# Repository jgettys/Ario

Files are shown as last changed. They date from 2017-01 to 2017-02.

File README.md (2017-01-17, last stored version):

# Ario

This is the mechanical design for ATMoB's ARIO 10' diameter telescope
dome.  It was designed by Charlie Gettys in the spring of 2016, and
fabricated by Charlie & Jim Gettys and Bruce Berger.  Note that we are
currently designing a radio controlled motor controller as a companion
to this mechanical design.

The design opens or closes the dome slit in approximately 30 seconds in
ideal circumstances.

Note: the specified threaded rod was ordered by mistake: it is gross
overkill for the application; something much cheaper can/should be
bought rather than the precision rod currently specified in the as
built BOM. And the corresponding nut used should also be much cheaper.

It may take 50-100lbs force to start the slit of 10' dome ATMoB
has; we may decide to improve the cable path on our dome using pully
sheaves (as many of the later versions of that dome already have
improved designs) to reduce the required force.

The clutch in the design should prevent over stressing of the cable.
The cable has an operating strength of about 90lbs, with a breaking
strength about five times higher.  The motor was sized to provide enough
torque to produce about 100lbs of force given the diameter of the
threaded rod.

The design could be adapted/scaled up for much larger dome slits or
roll off roofs, by choosing other motors or changing the gear ratio in
the drive.  The gearing used with the motor was deliberately chosen to
have that flexibility, and the motor itself is available in different
sizes.  The components are easily available and "standard" among the
FIRST robotics community.

There is a included spreadsheet for making the torque
computations. Note that the motor, gear box, cable and threaded rod
all interact to produce the desired speed and force to move the dome
slit.

This design could be scaled up by using larger threaded rods and cables.
The force and closing speed can also be changed over a significant range
by changing the gearing in the gear box.  The ARIO gear design order
is documented in the file "motorspec.txt".

At maximum torque, you should not choose a motor that will generate
more force than the operating strength of the chosen cable. The clutch
is intended to provide a "fail safe" such that the breaking strength
of the cable will never be reached.

At maximum torque of one of these motors, you may need to provide
significant current; 55 amps@12V for the chosen motor in the ARIO design.

We are currently designing a radio controlled remote dome motor
controller to go with this mechanical design to replace our existing
current limited power supply (which cannot provide enough current),
which will be driven by a deep cycle marine battery charged by a solar
panel on the dome, to avoid needing power transfer to the dome, which
may not be designed into most smaller domes. A battery can easily
provide the needed current for the limited time to open or close the
dome more easily than a power supply.

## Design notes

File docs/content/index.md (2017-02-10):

---
date: 2017-02-08T21:07:13+01:00
title: ATMoB Domus Dome Controller
type: index
weight: 0
---

## Modern, Open Source Design

Domus is a modern dome control system, intended to enable fully
automatic operation of a modern telescope, based on an elaboration of
the excellent work of Gerry Rozema's [NexDome system](https://github.com/grozzie2/NexDome).

Domus is very inexpensive and adaptable and is built from widely available components and all software and firmware is open source.

## Features

* "Fail Safe" operation: Domus is designed to enable safe unattended operation of a telescope. As such, the observatory must "fail safe" in case of:
    * Rain or mist conditions
    * Excessive Wind
    * Dewing conditions
* Adaptability to local telescope system
    * Wireless slit controller, enabling battery powered operation of the slit closing mechanism; no power and the dome will still be safed
    * Dome control via [ASCOM](http://ascom-standards.org), for Windows users
    * Dome control via [Indi](http://indilib.org/), for Linux and MacIntosh users
    * Dome control and customization via Web application
* Adaptability to a large variety of weather equipment, by using the [WeeWX](http://www.weewx.com/) software package
    * These include a large variety of USB weather stations, as well as some Ethernet based weather stations.
    * Custom rain/mist sensor, for "fail safe" operation of the dome

See the [getting started guide]({{< relref "getting-started/index.md" >}}) for instructions how to get
Domus up and running.

## Components

* Dome Slit Opening/Closing Mechanism
* Dome Rotation Mechanism
* Dome control electronics
* WeeWX weather software
* Weather station (select appropriate station from those supported by WeeWX)
* Raspberry Pi controller
    * To enable integration of the WeeWX weather system,
    * remote dome control,
    * interior and exterior cameras,
    * "fail safe" operation, so that malfunction of the telescope computer will not inhibit safing of the telescope.
    * (optional) local GPS stratum zero NTP server, to provide good time to the local observing environment
* Raspbian OS, configured for "headless" remote use via ssh or web operation
  
## Acknowledgements

Gerry Rozema designed the excellent [NexDome controller](https://github.com/grozzie2/NexDome)

Charlie Gettys designed the dome slit mechanism, with kibitzing from Jim Gettys, Alan Sliski, and [Bruce Berger](http://www.medomakretreatcenter.com/bruceberger.php).

[Alan Sliski](http://www.theskyscrapers.org/alan-sliski) designed the dome rotation mechanism and encoder, and the electronics for controlling the slit and dome, and integrated the weather sensor.

[Jim Gettys](https://en.wikipedia.org/wiki/Jim_Gettys) put together the control server, based on a Raspberry Pi, the WeeWX software, and glue.

The Web site design is due to the Hugo site generator, using the Material docs theme.

Furthermore, thanks to [Steve Francia](https://gihub.com/spf13) for creating Hugo and the [awesome community](https://github.com/spf13/hugo/graphs/contributors) around the project.

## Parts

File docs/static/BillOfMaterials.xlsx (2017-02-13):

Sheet: Dome Slit Mechanism
Name | Link | Unit Cost | Quantity | Total Cost | Notes
Mechanical:
100:1 Versa Planetary Gearbox with BAG Motor | http://www.vexrobotics.com/vexpro/motion/gearboxes/versaplanetary.html | $109.94 | 1 | $109.94 | Modular if we ever need to change ratio, though that seems unlikely.
Vex Robotics Shipping |  | $12.96 | 1 | $12.96
1/2" Shaft Diameter Torque Limiting Couplings | http://www.mcmaster.com/#torque-limiting-couplings/=124vc8c | $80.00 | 1 | $80.00 | Offered in 25, 50, 75, 100, 125 in-lb versions, can be adjusted +/- 10% of value
Bearing Blocks, 1/2" | http://www.mcmaster.com/#3813T12 | $6.51 | 2 | $13.02
Acme 3/4"-10 Threaded Rod | http://www.mcmaster.com/#99030A030 | $32.98 | 1 | $32.98 | This threaded rod is overkill; we need to select a much cheaper one
3/4"-10 Threaded Rod Nut | http://www.mcmaster.com/#95365A526 | $40.50 | 1 | $40.50 | This nut is also overkill: we need to select a cheaper one
McMasters Shipping |  | $30.00 | 1 | $30.00 | This is a guess, hopefully is less than this
Misc Hardware |  | $15.00 | 1 | $15.00 | Stainless steel cap head screws
.250 1/4" Mill Finish Aluminum Sheet Plate 6061 12" x 24" |  | $42.00 | 1 | $42.00 | Can be narrower, and probably less thick. We bought ours off of ebay for
100’ Flexible stainless steel cable | 3461T633 18-8 Stainless Steel Wire (https://www.mcmaster.com/) | $73.00 | 1 | $73.00 | Home center cable isn’t really flexible enough.
 |  |  | Subtotal: | $449.40
Estimated cost to replicate without current design mistakes: $400. |  |  |  | $400.00

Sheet: Weather Controller
Name | Unit Cost | Quantity | Total Cost | Notes
Raspberry Pi 3 Model B (http://www.canakit.com/raspberry-pi-3-model-b.html) | $35.00 | 1 | $35.00 | Other Pi’s could be used
Raspberry Pi Case (http://www.canakit.com/raspberry-pi-clear-case.html) | $9.95 | 0 | $0.00 | Case optional, other styles available
Raspberry Pi Adapter – 2.5A (Micro USB) (http://www.canakit.com/raspberry-pi-adapter-power-supply-2-5a.html) | $9.95 | 1 | $9.95 | Either this adapter or POE
PI PoE Switch HAT – Power over Ethernet (https://www.pi-supply.com/product/pi-poe-switch-hat-power-over-ethernet-for-raspberry-pi/) | $40.62 | 0 | $0.00 | Either POE adapter or Micro USB adapter
MicroSD card (16gb) | $8.40 | 2 | $16.80 | Whatever size you want/need; don’t forget backup! do not skimp on quality!
Shipping | $9.95 | 1 | $9.95
Ethernet cable | $3.00 | 1 | $3.00 | Length to plug into network
Subtotal |  |  | $74.70

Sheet: Weather Station
Name | Unit Cost | Quantity | Total Cost | Notes
Your choice of weather station; remember to get one compatible with WeeWX and that has interior temperature and humidity
Ambient Weather WS-1400-IP Observer (https://www.amazon.com/gp/product/B00O9YIEJW/ref=oh_aui_detailpage_o00_s00?ie=UTF8&psc=1) | $149.95 | 1 | $149.95 | Or other weather station: see WeeWX docs (http://www.weewx.com/hardware.html)
Mounting bracket (https://www.amazon.com/Ambient-Weather-EZ-30-12-Stable-Mounting/dp/B003EAANBO) | $44.99 | 1 | $44.99 | Depends on circumstances
Ethernet cable | $3.00 | 1 | $3.00 | Length to plug into network
Shipping | $14.55 | 1 | $14.55 | For the weather station only
Subtotal |  |  | $212.49

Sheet: Web Cams
Name | Unit Cost | Quantity | Total Cost | Notes
Interior Web Cam (IR) | $50.00 | 1 | $50.00 | Guess
Exterior Web Cam (regular) | $35.00 | 1 | $35.00 | Guess
Exterior housing | $20.00 | 1 | $20.00 | Guess
USB Cables | $3.00 | 2 | $6.00
Subtotal |  |  | $111.00

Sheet: Dome controllers
Name | Unit Cost | Quantity | Total Cost | Notes
Arduino Mega 2560 (https://www.adafruit.com/products/191) | $45.95 | 2 | $91.90
USB Cable | $3.00 | 1 | $3.00
Rain/Mist sensor (RG-11) (http://rainsensors.com/) | $59.00 | 1 | $59.00
Motor Controller (slit) (http://www.robotshop.com/en/cytron-single-10--45v-40a-brushed-dc-motor-controller.html) | $72.19 | 1 | $72.19
Motor Controller (dome) (http://www.robotshop.com/en/cytron-single-10--45v-40a-brushed-dc-motor-controller.html) | $72.19 | 1 | $72.19
SPDT switch | $2.00 | 1 | $2.00
Encoder for dome | $29.00 | 1 | $29.00
Subtotal |  |  | $300.28

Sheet: Mounting boxes
Name | Unit Cost | Quantity | Total Cost | Notes
Dome slit controller mounting box | $50.00 | 1 | $50.00
Dome controller mounting box | $20.00 | 1 | $20.00
Deep cycle marine battery | $100.00 | 1 | $100.00 | Guess
Mounting bracket for battery | $20.00 | 1 | $20.00 | Estimate
10W Solar panel for recharging | $35.00 | 1 | $35.00 | Price 2/2017
Battery charger |  | 0 | $0.00 | Solar panels often come with battery chargers
Mounting hardware | $5.00 | 1 | $5.00
Subtotal |  |  | $230.00

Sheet: Optional POE
Name | Unit Cost | Quantity | Total Cost | Notes
Ubiquiti EdgeRouter X x ER-X-SFP-US (6 ports) (https://www.amazon.com/gp/product/B012X45WH6/ref=oh_aui_search_detailpage?ie=UTF8&psc=1) | $72.99 | 0 | $0.00
PI PoE Switch HAT – Power over Ethernet (https://www.pi-supply.com/product/pi-poe-switch-hat-power-over-ethernet-for-raspberry-pi/) | $40.62 | 0 | $0.00 | Either POE adapter or Micro USB adapter
Macroreer for Ubiquiti Gigabit RJ45 Copper SFP (https://www.amazon.com/Macroreer-Ubiquiti-Transceiver-Mini-GBIC-1000Base-T/dp/B01JUBXDPI) | $19.99 | 0 | $0.00 | If you want copper backhaul
SFP cable | $0.00 | 0 | $0.00 | Whatever you need for backhaul
Ubiquiti Networks 8-Port UniFi Switch, Managed PoE | $184.99 | 0 | $0.00 | Alternate for more ports
Subtotal: |  |  | $0.00
POE & SFP may be wise to simplify cabling and protect against lightning destroying more than necessary
Ports: | Raspberry Pi
 | Computer
 | Weather station
 | Main camera
 | Guide camera
 | Mount
 | Back haul

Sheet: Total Costs
Name | Unit Cost | Quantity | Total Cost | Notes
Dome Slit Mechanism | $400.00 | 1 | $400.00
Raspberry Pi Weather Controller | $74.70 | 1 | $74.70
Weather Station | $212.49 | 1 | $212.49
Web Cams | $111.00 | 1 | $111.00
Dome controllers | $300.28 | 1 | $300.28
Mounting boxes | $230.00 | 1 | $230.00
Optional POE |  |  | $0.00
Total |  |  | $1328.47

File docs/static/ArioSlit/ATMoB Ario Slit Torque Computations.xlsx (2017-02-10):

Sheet: Calculations
Large Shaft Diameter | 5/8" | 1/2" Driven end, 1 1/8" free end
Small Shaft Diameter | 0.364 | 1 1/4" Driven end
Worm Diameter | 0.75
Worm Threads/Inch | 10
Worm Length (inches) | 13
Mechanical Advantage | 2:1
Voltage (Measured): | 14
Current (Power supply Max): | 12
Max power: | 168 | (That the current power supply can support, assuming 100% conversion)
Thread Number: | 130 | Thus, 130 RPM goal to close in 1 minute
Standard Operating Conditions: |  | ~100lb to move by hand
Worm Force (lb): | 80 | 2:1 Mechanical advantage means this translates to 160 pounds of force on the dome
Worm Radius (in): | 0.3125
Output Torque (in-lb): | 25
Bad Weather Conditions:
Worm Force (lb): | 160 | 320 | T=rxF; T/r = F
Worm Radius (in): | 0.3125 |  | small r -> big F
Output Torque (in-lb): | 50 |  | used minimum r
Limit at 25-50 lb
Motor specs: | http://www.vexrobotics.com/217-3351.html

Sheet: Bill of Materials
Name | Link | Unit Cost | Quantity | Total Cost | Notes
Mechanical:
1/2" Shaft Diameter Torque Limiting Couplings | http://www.mcmaster.com/#torque-limiting-couplings/=124vc8c | $80.00 | 1 | $80.00 | Offered in 25, 50, 75, 100, 125 in-lb versions, can be adjusted +/- 10% of value
100:1 Gearbox with BAG Motor | http://www.vexrobotics.com/vexpro/motion/gearboxes/versaplanetary.html | $110.00 | 1 | $110.00 | Modular if we ever need to change ratio, though that seems unlikely.
Bearing Blocks, 1/2" | http://www.mcmaster.com/#3813T12 | $6.51 | 2 | $13.02
Acme 3/4"-10 Threaded Rod | http://www.mcmaster.com/#99030A030 | $32.98 | 1 | $32.98
3/4"-10 Threaded Rod Nut | http://www.mcmaster.com/#95365A526 | $40.50 | 1 | $40.50 | If necessary; current nut should be compatible, but who knows
Shipping |  | $30.00 | 1 | $30.00 | This is a guess, hopefully is less than this
Misc Hardware |  | $15.00 | 1 | $15.00
Vex Shipping |  | $12.96 | 1 | $12.96
 |  |  | Subtotal: | $334.46

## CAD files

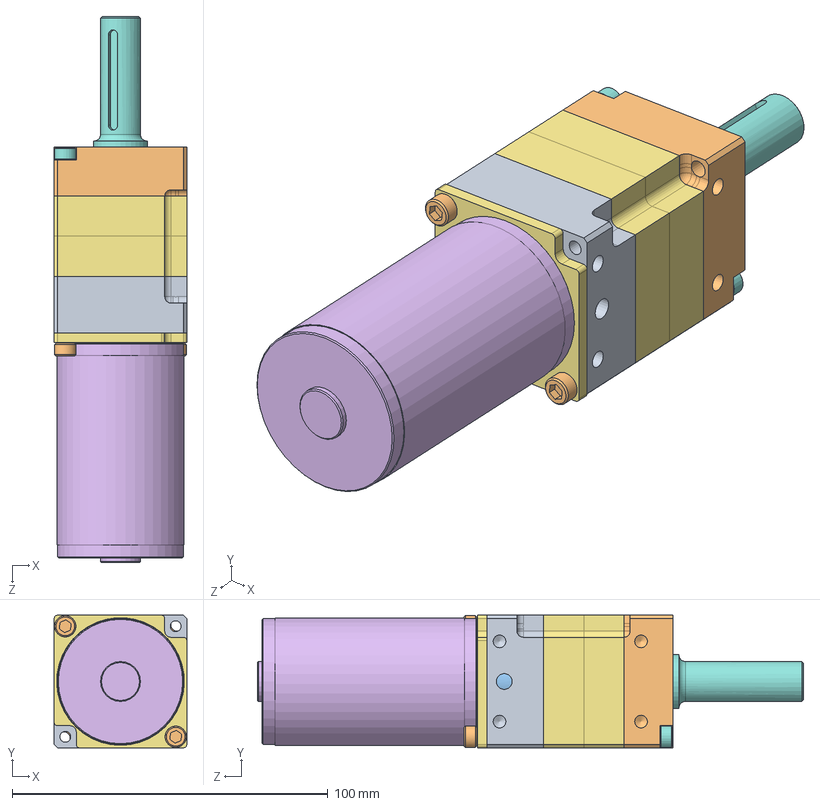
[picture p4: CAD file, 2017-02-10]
docs/static/ArioSlit/VEXpro-VersaPlanetary-2stage-with-BAG.sldasm
42.0 x 42.0 x 173.0 mm
217-2625-001 Rev1
217-2625-002 Rev1
217-2625-009 Rev1
217-2625-008 Rev1
217-2625-010 Rev1 x 7
217-2625-005 Rev1_Planet_Revolving_Follower01 x 3
217-2625-007 Rev1_Sun_Driver01
TRUARC-MSH-15_98541A410
SPRGW0856-1102-012_9714K62
SSS1032-0125ZB_94105A824
TRUARC-5103-68_97414A675_grv
217-2816-001 Rev1 x 2
SSA_SSA0832-1750ZC x 2
217-2625-011 Rev1
SSA_SSA0832-0500ZC x 2
SSHCM004_SSHCM004070010C x 2
217-2725-001 Rev1_24t Sun
217-2725-002 Rev1_24t Planet x 4
217-2724-002 Rev1
217-2822-003 Rev4
HalfInchKeyed

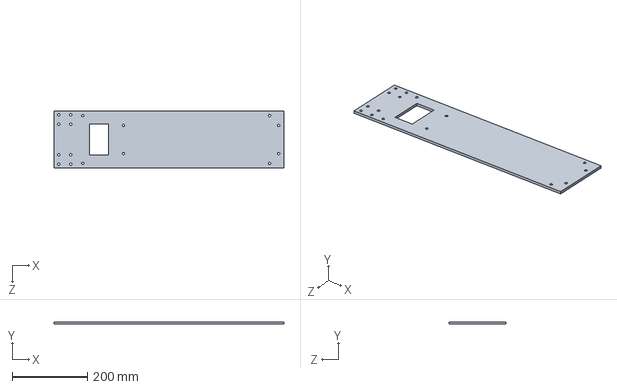
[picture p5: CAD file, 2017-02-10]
docs/static/ArioSlit/Main Plate.sldprt
609.6 x 6.35 x 152.4 mm

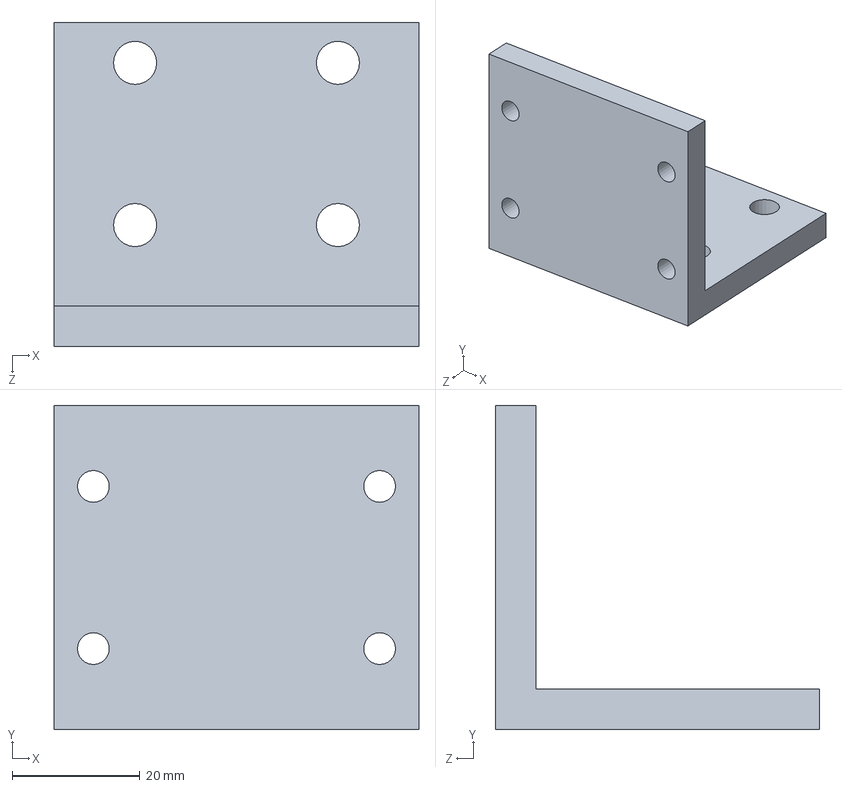
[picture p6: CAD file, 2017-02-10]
docs/static/ArioSlit/Bracket.sldprt
57.1 x 50.8 x 50.8 mm

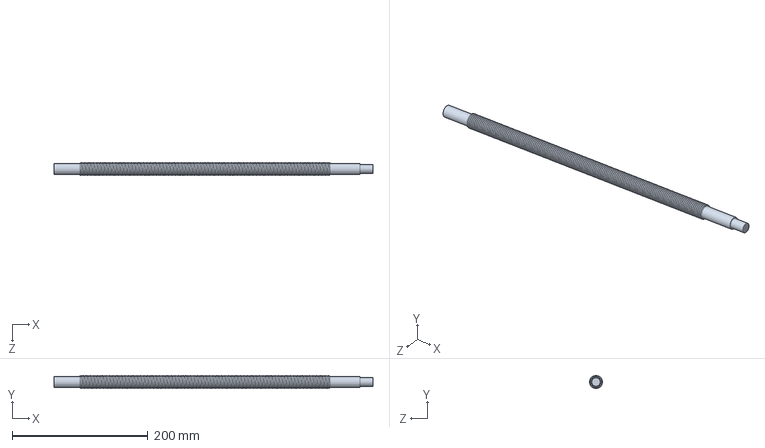
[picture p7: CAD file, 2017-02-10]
docs/static/ArioSlit/NewShaft.sldprt
469.9 x 19.0 x 19.0 mm

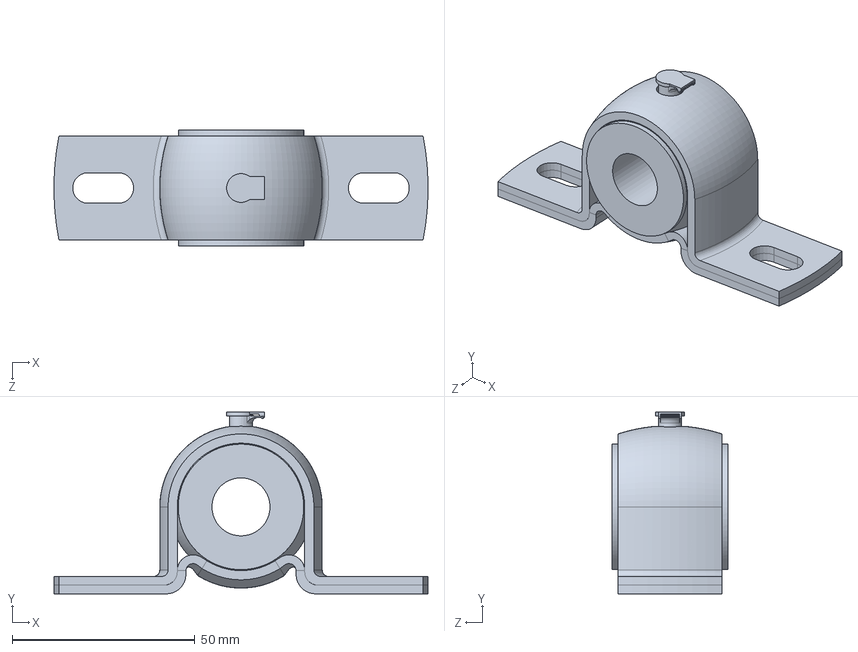
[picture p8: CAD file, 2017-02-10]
docs/static/ArioSlit/Bearing.sldprt
102.3 x 49.8 x 31.8 mm

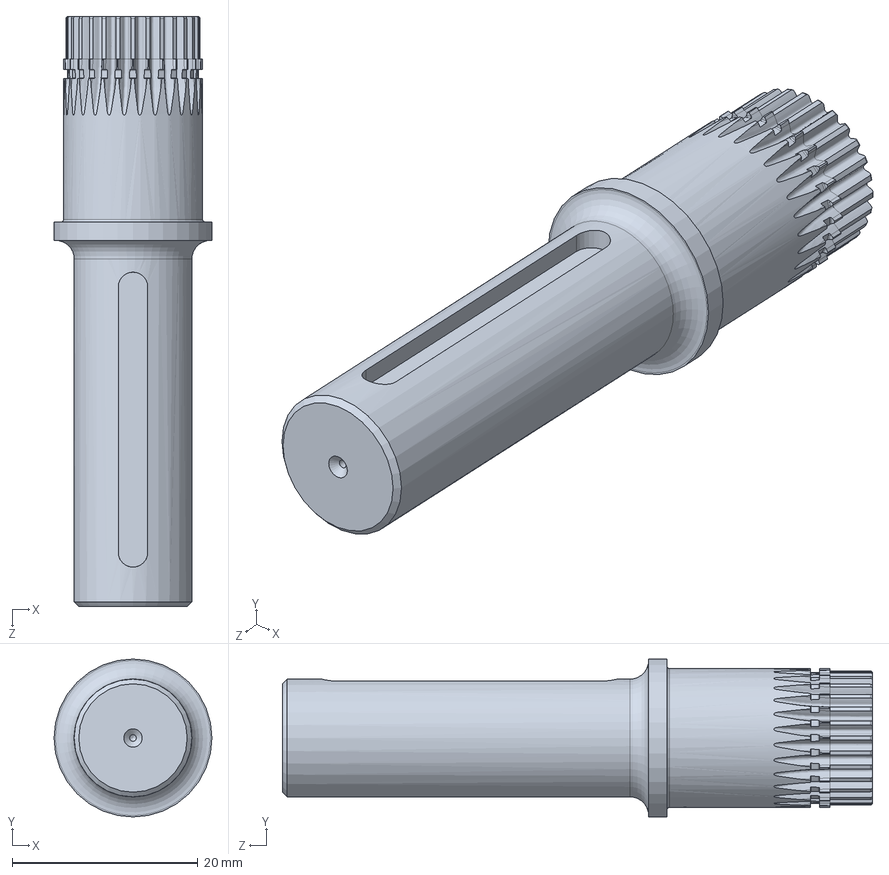
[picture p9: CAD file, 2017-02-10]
docs/static/ArioSlit/HalfInchKeyed.sldprt
17.0 x 17.0 x 63.5 mm

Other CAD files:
docs/static/ArioSlit/217-2625-100.sldasm
docs/static/ArioSlit/217-2818 Rev1.sldasm
docs/static/ArioSlit/TRUARC-5103-68_97414A675_grv.sldprt
docs/static/ArioSlit/SSS1032-0125ZB_94105A824.sldprt
docs/static/ArioSlit/217-2725-002 Rev1_24t Planet.sldprt
docs/static/ArioSlit/217-2822-003 Rev4.sldprt
docs/static/ArioSlit/TRUARC-MSH-15_98541A410.sldprt
docs/static/ArioSlit/217-2741.sldprt
docs/static/ArioSlit/217-2625-007 Rev1_Sun_Driver01.sldprt
docs/static/ArioSlit/SSA_SSA0832-0500ZC.sldprt
docs/static/ArioSlit/217-2625-010 Rev1.sldprt
docs/static/ArioSlit/217-2724-002 Rev1.sldprt
docs/static/ArioSlit/217-2625-001 Rev1.sldprt
docs/static/ArioSlit/217-2625-002 Rev1.sldprt
docs/static/ArioSlit/217-2625-005 Rev1_Planet_Revolving_Follower01.sldprt
docs/static/ArioSlit/217-2625-008 Rev1.sldprt
docs/static/ArioSlit/217-2625-009 Rev1.sldprt
docs/static/ArioSlit/217-2625-011 Rev1.sldprt
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

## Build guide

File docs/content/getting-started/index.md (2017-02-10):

---
date: 2017-01-09T00:11:02+01:00
title: Getting started
weight: 10
---

## Installation

### Installing Dome Slit Controller

To ensure "fail safe" operation of the dome, an Arduino based dome
slit controller is installed in a small box on the dome, along with a
battery able to open and close the dome. The Arduino drives a motor
controller to control the slit motor. A solar panel can be installed
on the outside of the dome to recharge the battery.

We recommend deep cycle marine batteries for this purpose, with enough
capacity that long periods of cloudy daytime weather do not interfere
with dome operations.

(XXX battery sensor?)

The dome slit controller Arduino communicates to the dome controller
Arduino via a wireless connection (XXX what type?). A "keep alive"
command is sent periodically to it from the dome controller; if it
fails for any reason to recieve this keep alive signal, it will
automatically close the dome. (XXX after a short delay???)

The dome slit controller Arduino is also connected to a (XXX what
type?) rain/mist sensor mounted on the outside of the dome. If rain or
mist is detected, the dome will be automatically closed (unless
inhibited).  This signal is also relayed to the dome controller.  The
sensor should be mounted outside the dome so that after a suitable
delay of no rain or mist sensed (XXX how long?), observing can be restarted.

### Install Dome Controller & Raspberry Pi system.

The dome controller Arduino and Raspberry Pi is mounted in a box in
the dome and powered from observatory power (or from POE???). It
communicates via wireless to the dome slit controller.

Your dome encoder must be mounted so that the encoder will detect dome motion.
The dome encoder is connected to the dome control Arduino.

A USB interface is provided to enable ASCOM and Indi operation.

(Someday I'll do ASCOM and Indi from the Pi.)

There are four USB connectors on the Raspberry Pi. These are used for:
1.  USB Webcam for interior    (alternatively, Ethernet web cams can be used)
2.  USB Webcam for exterior/sky (alternatively, Ethernet web cams can be used)
3.  ...

The Ethernet connector for the Raspberry Pi is connected to the
observatory's network.

### Install Weather Station

Choose an appropriate weather station for your purposes from those
[supported by WeeWX](http://www.weewx.com/hardware.html).

You should select a station which supports interior temperature and
humidity; these are used to warn of dewing conditions and cause an
automatic shutdown. Most convenient are those stations which report
these values wirelessly to a base station, allowing for flexible
placement of these sensors.

Some weather stations use Ethernet to report their results and may
need additional configuration, but this also provides the maximum
flexibility in weather station placement, since USB cables are limited
to less that 5 meters.

WeeWX will keep a database of your weather information, and can be
configured to report your weather to one or more popular weather
services such as [Weather
Underground](https://www.wunderground.com/weatherstation/overview.asp),
[Open Weather Map](https://openweathermap.org/stations), and other
weather services. Weather information is very useful in interpreting your
data later.

### Install Interior Humidity and Temperature Sensors

If you have a known location that tends to dew before other locations
in your observatory dome, install the interior humidity and
temperature sensors there.

### Install Interior and Exterior Cameras

An interior camera is important to confirm that the telescope is
pointing where you think it is, independently of your TCS (telescope
control program).

An exterior camera is very useful for monitoring sky conditions.

## Setup

Install software.

## Configuration

Edit the *XXXX file* for your system.

Configure WeeWX for your weather station.

Make a backup of your Raspberry Pi's flash card and save in a safe place
where you can find it.

Note that database writes can limit the length of lifetime of your
Raspberry Pi's flash card if this database locally on the Raspberry
Pi's flash card. If you configure a remote database on a computer
system (preferably one with regular backups), this problem can be
entirely avoided. Alternatively, configure the database onto a disk
drive you add to the Raspberry Pi via a USB port.

## Backups

Make a backup of your Raspberry Pi's flash card and save in a safe place
where you can find it.

The following packages are necessary for preservation of your configuration:
* XXX package list here.

The following files are modified from Raspbian to support this installation:
* XXX file list here.

## Options

### Github integration

If your project is hosted on GitHub, add the repository link to the
configuration. If the `provider` equals **GitHub**, the Material theme will
add a download and star button, and display the number of stars:

```toml
[params]
  # Repository
  provider = "GitHub"
  repo_url = "https://github.com/jgettys/Ario"
```

### Adding a logo

If your project has a logo, you can add it to the drawer/navigation by defining
the variable `logo`. Ideally, the image of your logo should have
rectangular shape with a minimum resolution of 128x128 and leave some room
towards the edges. The logo will also be used as a web application icon on iOS.
Either save your logo somewhere in the `static/` folder and reference the file relative to this location or use an external URL:

```toml
[params]
  logo = "images/logo.png"
```

### Adding a custom favicon

Favicons are small small icons that are displayed in the tabs right next to the title of the current page. As with the logo above you need to save your favicon in `static/` and link it relative to this folder or use an external URL:

```toml
[params]
  favicon = "favicon.ico"
```

### Google Analytics

You can enable Google Analytics by replacing `UA-XXXXXXXX-X` with your own tracking code.

```toml
googleAnalytics = "UA-XXXXXXXX-X"
```

### Small tweaks

This theme provides a simple way for making small adjustments, that is changing
some margins, centering text, etc. The `custom_css` and `custom_js` option allow you to add further CSS and JS files. They can either reside locally in the `/static` folder or on an external server, e.g. a CDN. In both cases use either the relative path to `/static` or the absolute URL to the external ressource.

```toml
[params]
  # Custom assets
  custom_css = [
    "foo.css",
    "bar.css"
  ]

  custom_js  = ["buzz.js"]
```

### Changing the color palette

Material defines a default hue for every primary and accent color on Google's
material design [color palette][]. This makes it very easy to change the overall look of the theme. Just set the variables `palette.primary` and `palette.accent` to one of the colors defined in the palette:

```toml
[params.palette]
  primary = "red"
  accent  = "light-green"
```

Color names can be written upper- or lowercase but must match the names of the
material design [color palette](http://www.materialui.co/colors). Valid values are: _red_, _pink_, _purple_, _deep purple_, _indigo_, _blue_, _light-blue_, _cyan_, _teal_, _green_, _light-green_,
_lime_, _yellow_, _amber_, _orange_, _deep-orange_, _brown_, _grey_ and
_blue-grey_. The last three colors can only be used as a primary color.

Color palette

If the color is set via this configuration, an additional CSS file called
`palettes.css` is included that defines the color palettes.

### Changing the font family

Material uses the [Ubuntu font family](http://font.ubuntu.com) by default, specifically the regular sans-serif type for text and the monospaced type for code. Both fonts are loaded from [Google Fonts](https://www.google.com/fonts) and can be easily changed to other fonts, like for example Google's own [Roboto font](https://www.google.com/fonts/specimen/Roboto):

```toml
[params.font]
  text = "Roboto"
  code = "Roboto Mono"
```

The text font will be loaded in font-weights 400 and **700**, the monospaced
font in regular weight.

### Syntax highlighting

This theme uses the popular [Highlight.js](https://highlightjs.org/)
library to colorize code examples. The default theme is called
`Github` with a few small tweaks. You can link our own theme if you
like. Again, store your stylesheet in the `static/` folder and set the
relative path in the config file:

```toml
[params]
  # Syntax highlighting theme
  highlight_css  = "path/to/theme.css"
```

### Adding a GitHub and Twitter account

If you have a GitHub and/or Twitter account, you can add links to your
accounts to the drawer by setting the variables `github` and
`twitter` respectively:

``` toml
[social]
  twitter = ""
  github  = "digitalcraftsman"
```

### Adding menu entries

Once you created your first content files you can link them manually in the sidebar on the left. A menu entry has the following schema:

```toml
[[menu.main]]
  name   = "Material"
  url    = "/"
  weight = 0
  pre    = ""
```

`name` is the title displayed in the menu and `url` the relative URL to the content. The `weight` attribute allows you to modify the order of the menu entries. A menu entry appears further down the more weight you add. The `pre` attribute is optional and allows you to *pre*pend elements to a menu link, e.g. an icon.

Instead of just linking a single file you can enhance the sidebar by creating a nested menu. This way you can list all pages of a section instead of linking them one by one (without nesting).

You need extend the frontmatter of each file content file in a section slightly. The snippet below registers this content file as 'child' of a menu entry that already exists.

```yaml
menu:
  main:
    parent: Material
    identifier: <link name>
    weight: 0
```

`main` specifies to which menu the content file should be added. `main` is the only menu in this theme by default. `parent` let's you register this content file to an existing menu entry, in this case the `Material` link. Note that the parent in the frontmatter needs to match the name in `config.toml`.

`identifier` is the link that is shown in the menu. Ideally you choose the same name for the `identifier` and the `title` of the page. Again, `weight` allows you to change the order of the nested links in a section.

### Markdown extensions

Hugo uses [Blackfriday](https://github.com/russross/blackfriday) to process your content. For a detailed description of all options take a look at the [Blackfriday configuration](http://gohugo.io/overview/configuration/#configure-blackfriday-rendering) section in the Hugo documentation.

```toml
[blackfriday]
  smartypants = true
  fractions = true
  smartDashes = true
  plainIDAnchors = true
```

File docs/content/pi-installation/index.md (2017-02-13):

---
date: 2017-02-12T19:23:51-05:00
title: index
---
    install noobs
    install raspbian
    apt-get update
    apt-get dist-upgrade
    apt-get install emacs
    apt-get autoremove
    adduser jg
    add jg to /etc/group for where pi is.
    scp .ssh pi.local:
    mkdir src
    git clone git@github.com:jgettys/Ario.git
    adduser weewx

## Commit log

2017-01-17 update readme, put proper date on the License and add the BOM
    [BillOfMaterials.xlsx]
2017-01-17 work on the bom, the readme file, and motor/gearbox specification.
    Add photo of completed, mounted dome slit drive.
2017-01-17 Some cleanups and corrections.
    [BillOfMaterials.xlsx]
2017-02-10 Lots of documentation work, using hugo.
    [217-2625-001 Rev1.sldprt, 217-2625-002 Rev1.sldprt, 217-2625-005 Rev1_Planet_Revolving_Follower01.sldprt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]
2017-02-13 add BOM and pi installation directions files
    [BillOfMaterials.xlsx]
